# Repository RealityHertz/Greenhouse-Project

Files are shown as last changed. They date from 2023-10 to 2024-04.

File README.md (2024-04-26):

# Autonomous Greenhouse Project

## Executive Summary

With this project Team 2 proposes to create a greenhouse that can wirelessly and autonomously detect soil moisture, pH level, and nutrient level as well as carbon dioxide and nitrogen monoxide in the greenhouse's atmosphere along with the greenhouse's temperature and humidity. The greenhouse will also be able to autonomously detect the water level of an exterior water source and fill said reservoir when the level is too low as well as running a timed watering cycle for the plants. 

## Capabilities

This version of the project will be able to accurately measure the levels of nitrogen, phosphorus, and potassium in the greenhouse soil as well as the temperature, humidity, carbon dioxide, and nitrogen monoxide levels in the atmosphere. The project will also be able to detect the water level of an external reservoir that will alert when low and be able to refill when the alert is sent.

## Salient Outcomes

### 1. Soil Moisture, pH, and Nutrient Level Detection
- **Outcome:** Develop a system that provides real-time data on soil conditions, allowing for precise adjustments to watering schedules and nutrient applications. This could lead to optimized plant growth and reduced resource waste.

### 2. Atmospheric Monitoring (CO2 and NO2 Levels)
- **Outcome:** Implement sensors that continuously monitor and log the levels of CO2 and NO2. This data could be used to adjust ventilation, maintaining optimal air quality for plant health.

### 3. Temperature and Humidity Control
- **Outcome:** Create a responsive system that adjusts internal temperature and humidity based on preset thresholds. This could help in maintaining a stable environment that promotes plant health and productivity.

### 4. Water Level Monitoring and Reservoir Refilling
- **Outcome:** Design an automated system that detects low water levels in an external reservoir and alerts for manual intervention. This ensures a consistent water supply for the greenhouse, crucial for plant survival and growth.

### 5. Adjustable Lighting System
- **Outcome:** Implement a lighting system that can adjust the duration of grow light exposure based on Human-Machine Interface (HMI) inputs. This allows for flexible light management tailored to the growth stages and needs of different plant

### Documentation and Sign-offs
For detailed outcomes and progress on these subsystems, refer to the specific documentation and sign-offs provided in the project's [Documentation/Signoffs folder](https://github.com/RealityHertz/Greenhouse-Project/tree/main/Documentation/Signoffs). This folder contains detailed reports and approval documents that outline the performance and expectations for each subsystem.

## Project Demonstration & Images

[Demonstration Videos](https://github.com/RealityHertz/Greenhouse-Project/tree/main/Documentation/Images/Team2_Experimental_Videos)

### Lighting System Images

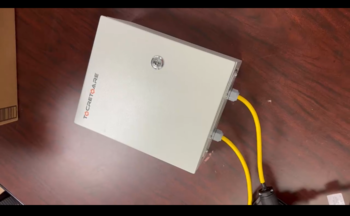
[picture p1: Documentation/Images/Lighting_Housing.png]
Lighting Housing


- The above image shows the housing for the lighting system as it is closed and being tested.

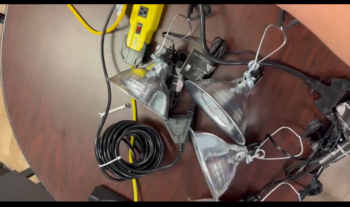
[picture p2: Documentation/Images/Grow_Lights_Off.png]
Grow Lights Off


- This image shows the lighting system's grow lights when they are powered off.

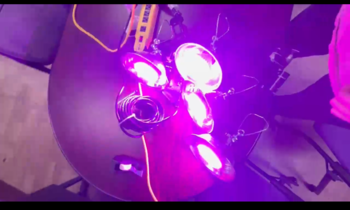
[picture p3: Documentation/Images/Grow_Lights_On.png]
Grow Lights On


- This shows the grow lights while powered on.

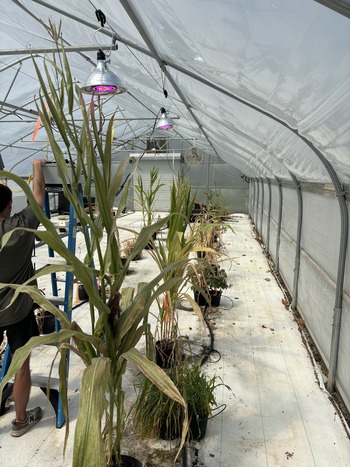
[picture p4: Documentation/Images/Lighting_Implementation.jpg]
Lighting Implementation


- This image shows the lighting system being implemented and tested within the greenhouse setting of the Hyder-Burks facility.

### PLC and HMI Images

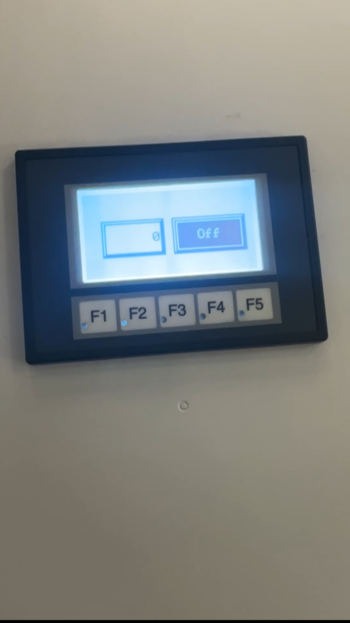
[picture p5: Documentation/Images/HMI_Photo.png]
HMI


- This shows the HMI as it rests within the PLC housing and is being tested.

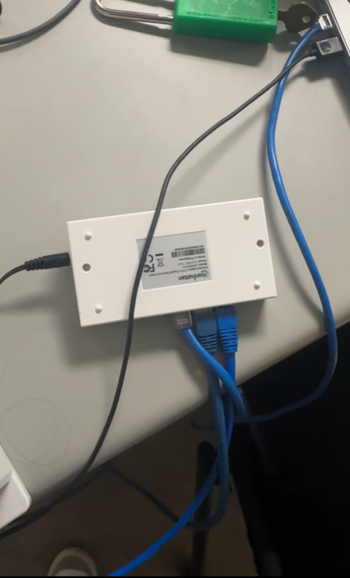
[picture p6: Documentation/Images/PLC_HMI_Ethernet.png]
PLC Ethernet Hub


- This image shows the ethernet hub that connects the PLC and HMI to an outside source for pushing of code and testing while powered on.

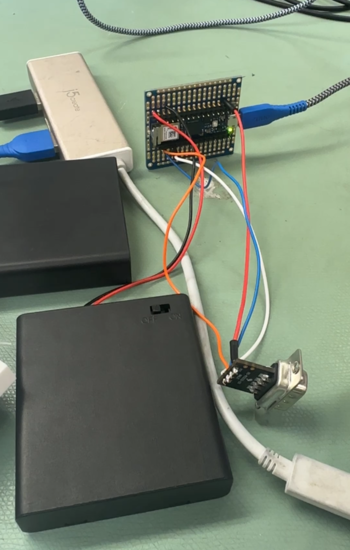
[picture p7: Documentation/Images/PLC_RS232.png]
PLC RS232 Translator
 

- The image above shows the RS232 to TTL translator module that allows the PLC to communicate with the Arduino pictured to allow for sending of commands and recieving of data.

### Water Level System Images

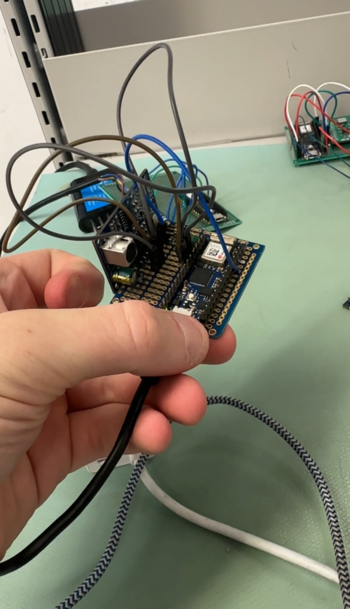
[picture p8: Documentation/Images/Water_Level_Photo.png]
Water Level Image


- Pictured above is the breadboard containing the water level sensor and the Arduino Nano 33 IoT for the water level system as it is being tested.

### CO2 and NO2 System Images

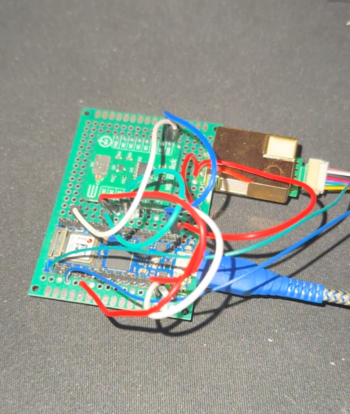
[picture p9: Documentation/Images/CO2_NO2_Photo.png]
CO2 and NO2 Image


- The above image shows the breadboard containing the carbon dioxide and nitrogen dioxide sensors for the CO2 and NO2 system as well as their connected Arduino. The nitrogen dioxide sensor is the green sensor pictured in the center of the image directly above the Arduino while the carbon dioxide sensor is the gold sensor located on the right hand side of the board.

### Temperature and Humidity System Images

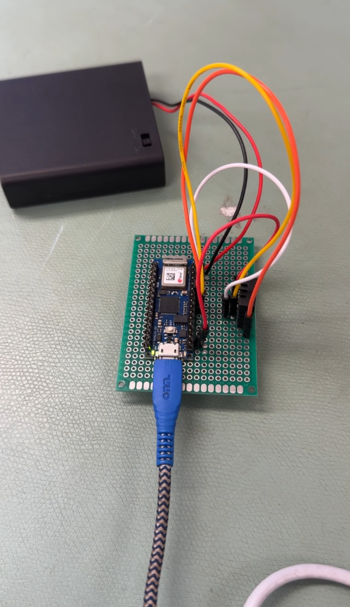
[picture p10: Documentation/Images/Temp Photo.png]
Temp and Humidity Image


- Pictured above is the temperature and humidity system with the transmitting Arduino pictured on the left of the board and the sensor itself pictured on the right as the small black box surrounded by wires.

### Nutrient System Images

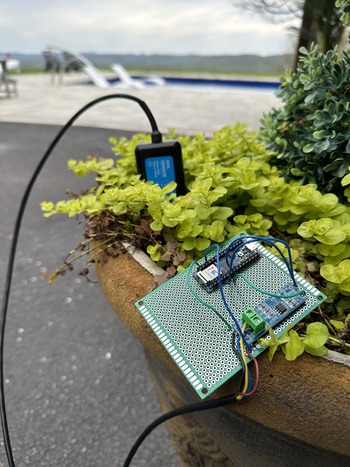
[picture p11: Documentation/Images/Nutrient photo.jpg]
Nutrient Image


- This image shows the nutrient monitoring system as it is being implemented in a pot of soil picturing the sensor placed in the soil, the Arduino for sending and recieving data and finally the MAX485 to TTL translator which is pictured on the far right of the board.

## About Us

### Team

Team 2 is a 5 member Capstone Design Project Team at Tennessee Technological University who began Version 1 of the Greenhouse Automation Project in the Fall semester of 2023. The group members are Robert Jones, Jared Hooker, Jaxson Billings, Bryan Rhoton, and Grant Hooper. All members contributed to the C02 and N02 Monitoring System.

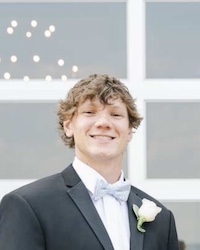
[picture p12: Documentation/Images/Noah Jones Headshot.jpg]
Noah Headshot

- **Robert Jones**
  - Electrical Engineering Major
  - Hardware
  - Controls
  - Lighting Control System
 
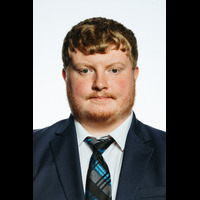
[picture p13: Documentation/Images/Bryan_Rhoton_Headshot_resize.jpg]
Bryan Headshot

- **Bryan Rhoton**
  - Computer Engineering Major
  - Soil Detection System

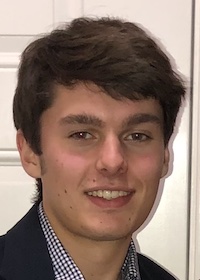
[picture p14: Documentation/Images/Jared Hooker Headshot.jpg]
Jared Headshot

- **Jared Hooker**
  - Electrical Engineering Major
  - Controls
  - Temperature & Humidity Monitoring System

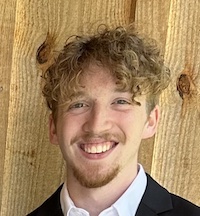
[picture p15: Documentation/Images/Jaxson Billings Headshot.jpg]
Jaxson Headshot

- **Jaxson Billings**
  - Computer Engineering Major
  - Programming
  - Communication and Display Subsystem

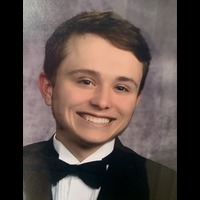
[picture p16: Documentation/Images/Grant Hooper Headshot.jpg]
Grant Headshot

- **Grant Hooper**
  - Electrical Engineer
  - Controls
  - Water Level Monitoring System

### Faculty Supervisor

The faculty advisor for the project is Jesse Roberts.

### Stakeholders

The customer for this project is the Agricultural Department at Tennessee Technological University. A scalable version of this design would be useful for agricultural researchers, farmers, and/or urban growers.

### Recognitions

Team 2 would like to recognize the sponsor for this project, EOSYS. They have worked closely with the group to help provide feedback, troubleshoot, and brainstorm ideas for the project. 

## Repo Organization

### [Reports](https://github.com/RealityHertz/Greenhouse-Project/tree/main/Reports)

Finalized reports can be found by going to the Reports folder or by clicking the link above.

### [Documentation](https://github.com/RealityHertz/Greenhouse-Project/tree/main/Documentation)

Group documentation can be found by going to the Documentation folder or by clicking the link above.

### [Software](https://github.com/RealityHertz/Greenhouse-Project/tree/main/Software)

Software can be found by going to the Software folder or by clicking the link above.

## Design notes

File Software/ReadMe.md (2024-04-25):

# Software Folder

This folder contains all of the software used in the Autonomous Greenhouse project. These files are required components representing background programming used in the subsystems within the greenhouse environment.

## Contents

- ArduinoIDE Folder
  -  Arduino_AHTXO
      -  File for DHT and AHT collection of data and BLE transmisson
  -  Arduino_CO2
      - File for MH-Z19B data collection and BLE transmisson
  -   Arduino_DHT
      - File for DHT20 data collection and BLE transmisson    
  -   Arduino_Lighting
      - Simple Digital Pin set high, delay, set low code to power the lighting   
  -   Arduino_NO2_w_ADC
      - File for MIKROE-3700 data collection and BLE transmisson   
  -   Arduino_NPK
      - File for NPK Sensor data collection and BLE transmisson
  -   Arduino_NPK_NoBLE
      - File for MH-Z19B data collection without BLE transmisson
  -   Arduino_NPK_NoBLE_From_Web
      - Test file for MH-Z19B data collection
  -   Arduino_RS232
      - File for transmisson through RS232 after data collection
  -   Arduino_Water_Level
      - File for distance sensor data collection and BLE transmisson and sends a true or false depending on how high or low the distance is
  -   Arduink_waterLevel
      - File for water level sensor data collection and BLE transmisson
  -   BLE_Scan_Test
      - File for the central Arduino that then sends the collected BLE data through RS232 to the PLC  
  -   NO2_SPI_Sensor
      -   File for MIKROE-3700 data collection and BLE transmisson through SPI.

## Usage

These software files represent the background programming that the subsystems need to function. This includes, but is not limited to, Arduino sleep pattern coding, sensor reading conversions, and sleep pattern timing. Refer to individual software directories for more information of each software's individual purpose and usage.

## File Formats

The software is provided in commonly used file formats compatible with the chosen arduino and sensors. Formats include `.c`, `.h`, and `.ino`.

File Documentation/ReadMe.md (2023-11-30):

# Documentation

The `Documentation` folder serves as a comprehensive repository of essential project documentation and artifacts for the Autonomous Greenhouse project. This README aims to provide guidance and an overview of the contents within this directory.

## Contents

### Signoffs

This directory contains markdown files for signoffs of subsystems. Each signoff document details the subsystem's purpose, constraints, buildable schematic, analysis, Bill of Materials (BOM), and more. Refer to the README in the "Signoffs" directory for detailed guidelines on creating and updating signoff files.

### Final Set of Prints (Final Design Artifacts)

All schematics and design artifacts, including 3D models, wiring schematics, PCB files, final BOM, datasheets, project poster, detailed project photos, and any additional relevant documents, are stored here.

#### 3D Models

Stored in `.stl` format, these models provide complete, buildable 3D representations of the various systems within the project.

#### Wiring Schematics

Electrical systems' wiring schematics, created using AutoCAD or AutoCAD Electrical, are stored here. Source files and PDF versions of the schematics must be included.

#### PCB Files

KiCad is used for all PCB design, with source files and complete gerber files included. PCB-related documents are housed within this section.

#### Final BOM

A PDF output of the Excel-based Bill of Materials (BOM) file along with the Excel file itself is included here.

#### Datasheet

This document contains vital information necessary for interfacing with the project, including power expectations, interfacing details, compliance information, experimental results, and their interpretations.

#### Project Poster

The project poster, visually representing key project details and components, is stored in this section.

#### Detailed Photos

A folder of detailed project photos provides visual documentation of the project's various aspects.

#### Additional Documents

Any other pertinent documents relevant to understanding, working on, or with the project are included in this section.

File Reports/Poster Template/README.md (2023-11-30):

# Autonomous Greenhouse Poster

## Contents

- Currently empty. Poster coming Spring 2024.

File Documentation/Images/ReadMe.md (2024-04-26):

# Images Folder

The `Images` folder contains visual assets utilized in the markdown files detailing subsystem designs and resources needed within the `Sign-offs` folder within the Autonomous Greenhouse project.

## Contents

The images are organized based on alphabetical order. They are used in various subsystem design markdown files. They aid in visually explaining and illustrating different components and concepts of the subsystems.

### Images

- **3D-artifact-CAPSTONE.png**
- **3D-artifact-sensor-CAPSTONE.png**
- **3D-artifact-topdown-CAPSTONE.png**
- **AA-100mA.png**
- **ArduinoNano33.png**
- **Breaker Datasheet.png**
- **CADHMISubsystemSchematic.jpg**
- **CADPLCSubsystemSchematic.jpg**
- **CADSchematicNitrogenSubsystem.jpg**
- **CADTemperature&HumidityDrawing.jpg**
- **CADUPDATED.png**
- **CO2graph.png**
- **Cad Final Update.png**
- **Final Drawing Line.png**
- **Final Relay Data.png**
- **Final Relay Pic.png**
- **HMI2DModel.PNG**
- **HMIMountingRearView.png**
- **HMIMountingSideView.png**
- **HMIScrewPlacement.png**
- **Jaxson Billings Headshot.jpg**
- **Lighitng Control Timing.png**
- **Mounting-Model.png**
- **NPK Sleep Mode.png**
- **NPK_Battery_Supply.png**
- **Noah Jones Headshot.jpg**
- **Nutrient_Off_Sim2.png**
- **Nutrient_On_Sim2.png**
- **Nutrient_Schematic_V7.png**
- **PLC 2D Model.png**
- **PLCPowerSupply2DCAD.PNG**
- **PPM.png**
- **PhopGraph.png**
- **PotaGraph.png**
- **Relay Datasheet.png**
- **RelayDiagram.png**
- **RelayPic.png**
- **SPIDataOutToINT.png**
- **Screenshot 2024-03-08 123324.jpg**
- **Tx to Int Code.png**
- **Updated paint.png**
- **VoltageGraph.png**
- **WaterLevelGraph.png**
- **Water_Level_Schematic.png**
- **pHGraph.png**
- **CO2_NO2_Photo.png**
- **Grow_Lights_Off.png**
- **Grow_Lights_On.png**
- **HMI_Photo.png**
- **Lighting_Housing.png**
- **Lighting_Implementation.jpg**
- **Nutrient Photo.jpg**
- **PLC_HMI_Ethernet.png**
- **PLC_RS232.png**
- **Temp Photo.png**
- **Water_Level_Photo.png**

## Usage

These images play a pivotal role in enhancing the understanding and visualization of the subsystem designs presented in the markdown files. Each subfolder corresponds to a specific subsystem and contains relevant images associated with that subsystem's design documentation.

## File Formats

The images are available in formats such as `.png`, `.jpg`, `.svg`, or other common image formats, ensuring compatibility across various markdown rendering platforms.

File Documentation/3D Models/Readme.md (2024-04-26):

# 3D Models Folder

This folder contains a collection of 3D models used in the Autonomous Greenhouse project. These models are integral components representing various elements used in subsystems within the greenhouse environment.

## Contents

- Mount for the water level monitoring system

## Usage

These 3D models serve specific purposes within the project, such as simulating greenhouse structures, equipment, or plant elements. Refer to the individual model directories for more detailed information on each model's application and usage.

## File Formats

The models are provided in commonly used file formats compatible with standard 3D modeling software. Format on all 3D models is `.stl`.

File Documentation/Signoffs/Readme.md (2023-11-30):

# Signoffs Folder

The `Signoffs` folder holds signoff markdown files for each subsystem within the Autonomous Greenhouse project. These files adhere to specific guidelines for submitting and updating signoffs as outlined below.

## Content

  - **CO2 & NO2 Monitoring Subsystem Signoff**
  - **Lighting Control Subsystem Signoff**
  - **Display Subsystem Signoff**
  - **Water Level Subsystem Signoff**
  - **PLC Subsystem Signoff**
  - **Nutrient Monitoring Subsystem Signoff**
  - **Temperature & Humidity Monitoring Subsystem Signoff**

## Sections in Signoff Markdown File

Each signoff markdown file must include the following sections:

### Function of the Subsystem

Explain the primary function and role of the subsystem. Clarify its atomic purpose as outlined in the conceptual design.

### Constraints

Detail the constraints for the subsystem, explaining the rationale behind each constraint. Constraints may arise from physics, other subsystem requirements, standards, ethics, or socioeconomic considerations.

### Buildable Schematic

Embed a clear and appropriately sized schematic directly into the markdown file as a JPEG image. Ensure the schematic contains all necessary details for someone unfamiliar with the design to build it. Upload the actual design artifacts (e.g., 3D models, CAD files, gerber files) to the documentation folder in the appropriate location.

### Analysis

Provide a comprehensive analysis of the design, demonstrating how it meets the constraints and functions as intended. Ensure the analysis is well-explained and convincing to the faculty supervisor.

### Bill of Materials (BOM)

Include a markdown table listing all components required for the design, along with the cost of each component and the total cost of the subsystem.

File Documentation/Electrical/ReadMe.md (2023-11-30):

# Electrical Folder

This folder contains electrical designs and schematics related to various subsystems within the Autonomous Greenhouse project.

## Subfolders

### Schematics

The `Schematics` subfolder houses detailed designs of individual electrical subsystems. Each subsystem's schematic is categorized and stored within its respective directory.

### Contents

- **Display Subsystem**
- **Nitrogen and Carbon Dioxide Monitoring Subsystem**
- **Lighting Control Subsystem**
- **Temperature and Humidity Monitoring Subsystem**

## Usage

These electrical schematics are crucial for understanding and implementing the respective subsystems within the autonomous greenhouse setup. Navigate into each subsystem directory for comprehensive information on the electrical designs.

## File Formats

The schematics are in file formats such as `.jpg`, `.png`, `.svg`, or other common formats, allowing easy viewing and reference.

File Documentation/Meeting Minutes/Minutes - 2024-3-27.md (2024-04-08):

 

# *Meeting Minutes – Greenhouse Project* 

**Location:**

Brown 320

**Date:**

Wednesday, April 3rd

**Time:**

2:30 PM

**Attendance:**

Noah Jones

Grant Hooper

Jaxson Billings

Jared Hooker

Bryan Rhoton

**Agenda Items**

1\. Update Jesse on Minimally Functioning Subsystems

**Action Items**

1\. Use Serial and Manual for PLC

2\. Communication for PLC

3\. How the PLC communicate from the bus to the Ladder Logic is completely dependent.

**Individual Items**

Brian Rhoton: Work on Functional Prototype Design.

Grant Hooper: Work on Functional Prototype Design. PLC Ladder Logic.

Noah Jones: Work on Functional Prototype Design.

Jared Hooker: Work on Functional Prototype Design.

Jaxson Billings: Work on Functional Prototype Design. Weekly Minutes.

Group: Meet with EOSYS

**Other Notes**

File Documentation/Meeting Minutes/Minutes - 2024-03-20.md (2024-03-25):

 

# *Meeting Minutes – Greenhouse Project* 

**Location:**

Brown 320

**Date:**

Friday, March 22th

**Time:**

2:30 PM

**Attendance:**

Noah Jones

Grant Hooper

Jaxson Billings

Jared Hooker

Bryan Rhoton

EOSYS

**Agenda Items**

1\. Functional Prototype Design Constraints

2\. Week 10 Minutes.

**Action Items**

1\. Make sure all subsystems are plugged up and commuicating in a non-trival manner. Box needs to be closed and lighting or everything turned off to open it.

2\. NO2 Sensor is Functional.

3\. Arduino's are communicating via BLE.

4\. CO2 Sensor is functional.

**Individual Items**

Brian Rhoton: Work on Functional Prototype Design.

Grant Hooper: Work on Functional Prototype Design. PLC Ladder Logic.

Noah Jones: Work on Functional Prototype Design.

Jared Hooker: Work on Functional Prototype Design.

Jaxson Billings: Work on Functional Prototype Design. Weekly Minutes.

Group: Meet with EOSYS

**Other Notes**

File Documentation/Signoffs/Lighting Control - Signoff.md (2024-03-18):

 

# *Detail Design: Lighting Control*
## **Team Members: Robert Jones**
## **Function of the Subsystem:**
The function of this subsystem is to have grow lights shine on the plants to help them in their growing process. The system will allow the full-spectrum light operating hours to be adjustable via the PLC and the programmable buttons on the HMI. The system will be controlled by an Arduino which is connected to the Programmable Logic Controller (PLC) subsystem to tell the lights when to turn on and off. 
## **Constraints:**
- **Lighting Timing**

	During a plant's photosynthesis process, they require between 12 and 16 hours a day of full spectrum light. On an average day, a plant inside of the greenhouse will only receive around 10 hours per day. [1] To combat this, the lights must be able to shine for a minimum of 2 hours per day.
- **Light Intensity**

	Most plants need between 200-400 µmol/m²/s of light intensity to help to achieve optimal plant growth. [2] To achieve this measure of success, the distance of the lights from the plants will have to be fully adjustable as the plants grow upward toward the lights.
- **Light Control**

	To make the lights controllable for the user, the HMI must give the user the ability to adjust how long the lights are on per day. This must be between 2 and 6 hours, based on the current weather conditions or any other factors that may reduce UV light on the plants.  

## **Buildable Schematic:**
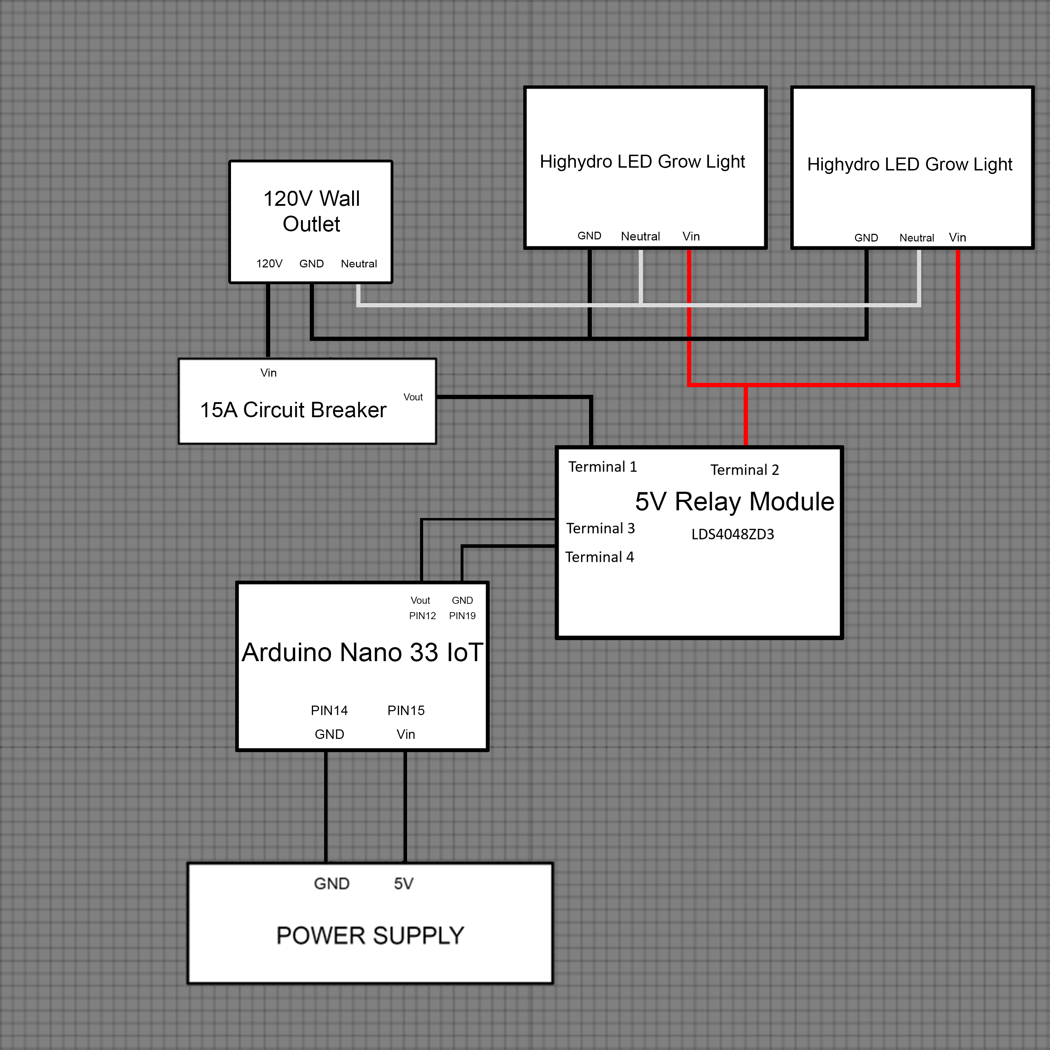
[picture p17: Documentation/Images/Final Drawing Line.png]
Lighting Control Schematic

*Figure 1. Buildable Schematic*

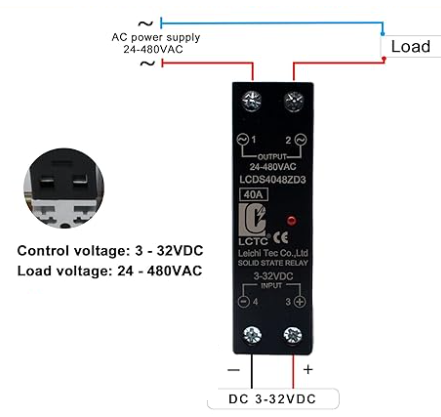
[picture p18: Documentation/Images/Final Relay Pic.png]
Relay Diagram


*Figure 2. Relay Diagram*

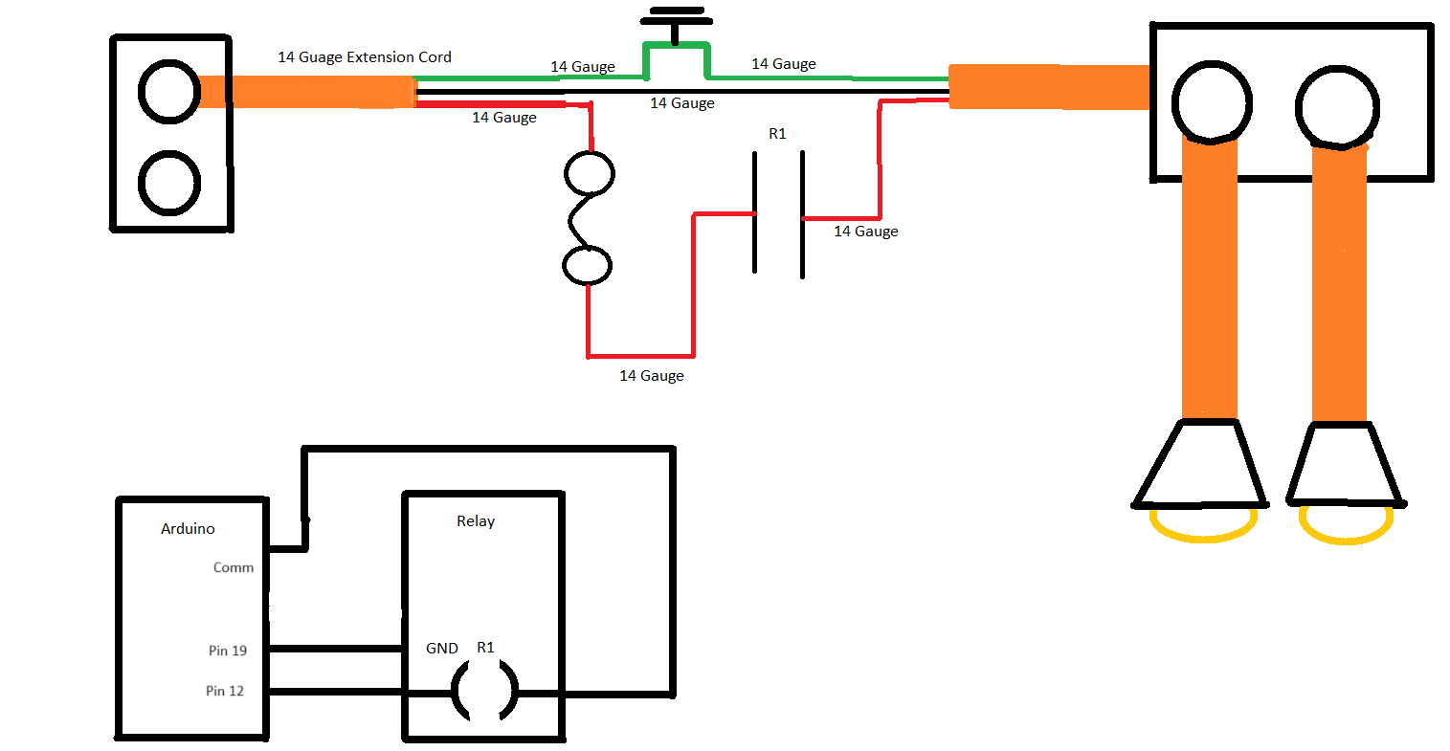
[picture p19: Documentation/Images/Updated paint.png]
Blueprint


*Figure 3. Connections*

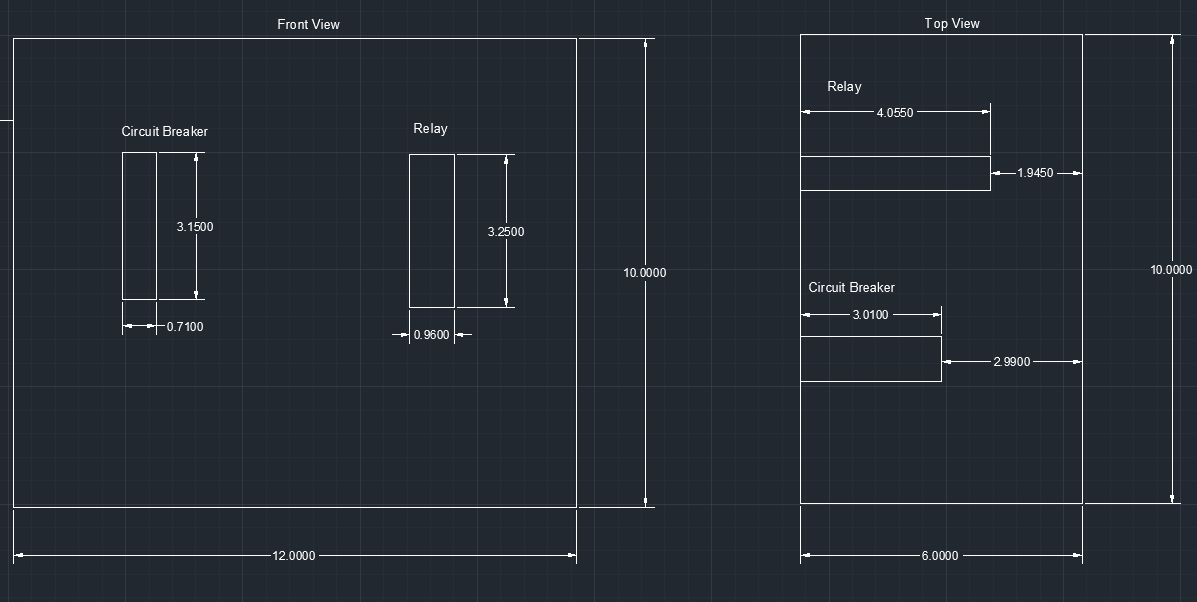
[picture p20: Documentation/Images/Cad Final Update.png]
NEMA 4X Enclosure Fit


*Figure 4. Enclosure Schematic. The figure on the right is the front view, with the left being the top view*
## **Analysis:**
- **Lighting Spectrum:**
1. The system uses four full-spectrum light bulbs which mimic UV rays from the sun. These lights will allow the plants to achieve optimal growth even when sunlight is not apparent.

- **Power Supply for Arduino Nano 33 IoT:**
 1. The power will be USB from a 120-volt wall outlet and will supply 5 volts to the Pin 15 on the Nano 33 IoT. The Pin 14 on the Nano 33 IoT will need to be connected to the ground from the USB ground wire.
 2. The USB cable and plug used have a max current of 1 amp and 2 amp respectively. This will allow for a safe current supply to the board.

- **Power Supply for Grow Bulbs:**
 1. The Arduino 33 Iot only has the ability to output 5V and a maximum current of 1 A, which will not satisfy the lights that need 100W.
 2.  A 15A breaker will be placed in the circuit to protect the wiring of the system. This breaker will meet the needs of the circuit based on: P=IV = 400W=I*120, therefore, the current is 3.33 amps which is below the rating of the 15A breaker.

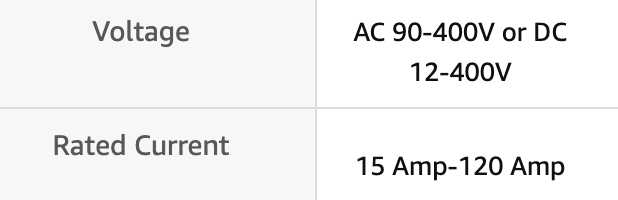
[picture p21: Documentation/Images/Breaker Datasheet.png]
Breaker Datasheet


*Figure 5. Breaker Datasheet*

 3. A relay will be placed in the circuit to control the main power while still allowing the Nano IoT to control the lights.[3]
 4. The relay has a maximum current rating of 40 A and a maximum voltage rating of 480 VAC. The system will be running on 120 VAC and 3.33A, therefore this relay meets the requirements.
 5. From the outlet, the power will be run through an extension cord to a NEMA 4x enclosure which will house the 15A circuit breaker and the relay.
 6. NEMA 4x was chosen due to its ability to keep out dust and direct sprays from water.
Here is an  excerpt from the Datasheet providing these requirements will be fulfilled:

Relay Data Sheet

*Figure 6. Relay Datasheet*

 7. Next, 14 gauge extension cords will be run from the relay to the lights. This will allow for safe power transfer due to the maximum amperage rating on the wire being 15 amps.[6]
 8. The positive wire of the extension cord, which is from the 120V wall outlet, will go into the breaker which will then come out of the other side of the breaker and into the common pin of the relay.
 9. The neutral wire will go straight to the extension cord which is connected to the lights, which allows for the unused power from the lights to return to the power supply.
 10. The ground wire will be grounded inside the box and also go to the lights, this is to ensure that the circuit will be shorted if there were to be a loose neutral or hot wire in the box.
 11. The bulbs will screw into an aluminum reflector lamp which will plug into the extension cord.

- **Enclosure Sizing and Mounting:**
1. The NEMA 4X enclosure is a 12x10x6 box which will house the circuit breaker and relay.
2. The circuit breaker is 0.71x3.15x2.95 and the relay is 0.96x3.25x3.01.
3. Therefore, these items will have a perfect fit inside of the enclosure and allow for plenty of space for the user to maneuver and to be able to run wires to each.
4. Each component inside of the enclosure will mount using DIN Mounting rails which are provided with the enclosure and both the relay and breaker can connect to.

- **Light Intensity:**
1. To give the plants the needed light intensity of 200-400 µmol/m²/s, the distance from the top of the plant to the light must be calculated.
2. Using the formula, Irradiance = Power/4π(r)^2, where P is equal to 100 watts for the bulb and r is equal to the distance of 5.5 feet from the top of the plant, the irradiance is equal to 318 µmol/m²/s, which is well within the range needed for cotton plants. [4]
3. Having the lights hung 5.5 feet above the plants will allow them to reach optimal growth, which is proven by the irradiance of the lights being 318 µmol/m²/s when 200-400 µmol/m²/s is needed. [2]
4. To achieve this constraint, the lights will be hung from a small chain and S-hook to be fully adjustable.

- **Control:**
1. To regulate the timing of light activation and deactivation, the HMI subsystem will feature four programmable buttons.
2. These buttons will enable users to adjust the duration for which the lights remain on and off, allowing for hour-by-hour increments in both directions.
3. For instance, if the preset timing is 2 hours for light activation and 8 hours for deactivation, the buttons will facilitate incremental adjustments, allowing users to increase or decrease each timing by one hour as needed.
4. To add further capabilities, a photocell will be added to the PLC to tell the system if it is day or night. This will in turn allow the PLC to know when the light should start the cycle that has been set by the user.

## **Bill of Materials:**
|Brand/Manufacturer|Part Name|Supplier|Part/Model Number|Quantity|Individual Price|Total|
|----|---|---|---|---|---|-----|
|LCLCTC|Relay Module|Amazon|B0BQ2RFW6G|1|$18.90|$18.90|
|Highydro|Full Spectrum Grow Light|Amazon|Grow Light|4|$21.99|$87.96|
|Arduino|Bluetooth Board|Amazon|Nano 33 IoT|1|$25.90|$25.90|
|VIVOSUN|4 Pack Lamp Aluminum Reflector E26|Amazon|B07H8G6PKX|1|$22.99|$22.99|
|DIHOOL|15 Amp Circuit Breaker|Amazon|B0BFF6CX2X|1|$13.99|$13.99|
|AIRIC|Cable Glands|Amazon|NPT 1/4" 20 Pieces|1|$11.99|$11.99|
|TOCRETOARE|NEMA 4x Enclosure|Amazon|12x10x6" Box|1|$49.99|$49.99|
|HONDERSON|10ft 14-3 Extension Cord|Amazon|3 Prong SJTW Heavy Duty Extension Cable|1|$12.99|$12.99|
|Maximm|30ft 14 Gauge Extension Cord with Multiple Outlets|Amazon|B0BT56KZCR|1|$32.99|$32.99|
|Leviton|Straight Blade Rubber Plug|Amazon|000-515PR-000|1|$7.25|$7.25|

## **References:**

[1]
Everbeam. “How Long to Leave UV Light on Plants: A Guide to Optimal Exposure Time.” Everbeam, shopeverbeam.com/blogs/news/how-long-to-leave-uv-light-on-plants-a-guide-to-optimal-exposure-time#:~:text=The%20distance%20between%20the%20plants%20and%20the%20grow. Accessed 13 Feb. 2024.

[2]
H. Chen et al., “Competition for Light Interception in Cotton Populations of Different Densities,” Agronomy, vol. 11, no. 1, p. 176, Jan. 2021, doi: 10.3390/agronomy11010176. [Online]. Available: http://dx.doi.org/10.3390/agronomy11010176
‌

[3]
Cruz, Terenz Jomar Dela. “How to Power Light Bulbs Using an Arduino with a Relay Module.” IoT Tech Trends, 19 Oct. 2022, www.iottechtrends.com/use-relay-module-with-arduino/.

[4]
How Close Should Grow Lights Be to Plants? 22 Apr. 2023, theindoornursery.com/blog/how-close-should-grow-lights-be-to-plants/#:~:text=In%20general%2C%20grow%20lights%20for%20mature%20plants%20should. Accessed 13 Feb. 2024.

[5]
Vanorio, Ame. “Growing Cotton: A Complete Guide on How to Plant, Grow, & Harvest Cotton.” MorningChores, 24 July 2019, morningchores.com/growing-cotton/.

[6]
National Electrical Code Basics: Sizing and protecting branch-circuit conductors - technical articles. EEPower. (n.d.). https://eepower.com/technical-articles/national-electrical-code-basics-sizing-and-protecting-branch-circuit-conductors

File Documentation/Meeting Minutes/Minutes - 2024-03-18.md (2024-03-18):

 

# *Meeting Minutes – Greenhouse Project* 

**Location:**

Brown 320

**Date:**

Monday, March 18th

**Time:**

2:30 PM

**Attendance:**

Noah Jones

Grant Hooper

Jaxson Billings

**Agenda Items**

1\. Sign-off/Revise Light Control Subsystem.

2\. Understand what is needed for Functional Prototype Design.

3\. Week 8 Minutes.

**Action Items**

1\. Lighting Subsystem Signed off.

2\. Make sure all subsystems are plugged up and commuicating in a non-trival manner. Box needs to be closed and lighting or everything turned off to open it.

**Individual Items**

Brian Rhoton: Work on Functional Prototype Design.

Grant Hooper: Work on Functional Prototype Design.

Noah Jones: Work on Functional Prototype Design. Blue LEDs are hard to get.

Jared Hooker: Help with other subsystems.

Jaxson Billings: Revise Sign-off Lighting Subsystem. Meeting minutes.

Group: Meet with EOSYS

**Other Notes**

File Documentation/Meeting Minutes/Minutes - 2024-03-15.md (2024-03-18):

 

# *Meeting Minutes – Greenhouse Project* 

**Location:**

Brown 320

**Date:**

Friday, March 6th

**Time:**

2:30 PM

**Attendance:**

Noah Jones

Jared Hooker

Grant Hooper

Bryan Rhoton

**Agenda Items**

1\. Sign-off/Revise Light Control Subsystem

2\. Sign-off/Revise Water Level Control Subsystem

3\. Week 8 Minutes.

**Action Items**

1\. HMI Subsystem Signed off.

2\. Nutirent Subsystem Signed off.

3\. Check in with EOSYS.

**Individual Items**

Brian: found a different sensor to measure at 5V and took away the regulator. Still communicates using RS485. Sensor will be running for 3 months according to the calculations. Jesse asked how long the batteries would actually last when considering battery decay.

 - “System is very vulnerable to the voltage dropping”. -Jesse

 - “Leaving tons and tons of charge in the batteries”

 - How can we boost the batteries to ensure that 5V is always attainable for an accepted amount of time? (3 months)

Grant: sensor communicates with PWM.

 - Find the pin on the Arduino that can be used for GPIO input PWM.

 - What is the frequency of the PWM?

 - Reverse engineer the code to understand how they got the frequency.

Noah: possibly draw the schematic on paper or in the Paint software

 - Break the ground to the box

 - Discussed the schematic with Jesse, he showed us an ideal way to make the schematic

Jared Hooker: Help with other subsystems.

Jaxson Billings: Revise Sign-off Lighting Subsystem. Meeting minutes.

Group: Meet with EOSYS

**Other Notes**

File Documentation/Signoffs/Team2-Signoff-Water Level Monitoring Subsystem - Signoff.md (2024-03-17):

# **Detail Design: Water Sensor**

## **Function of the Subsystem:**

The function of this subsystem is to relay the water levels to the Arduino via their respective sensors. The subsystem will use a sensor to determine whether the water reservoir is empty or not. If the reservoir is low on water, it will send data to the PLC for it to be refilled. The system is also able to be turned off for the user to manually water the plants.

## **Constraints:**

- **Arduino Nano 33 IoT**
  - The communication between the sensors and PLC system must be wireless. This will save time and money on wiring, while also allowing the system to be scalable.
  - The transfer of data between the sensors and the Arduino must be below 3 seconds for accurate and reliable monitoring of water level.
  - BLE (Bluetooth Low Energy) is lower in cost than the classic Bluetooth as BLE is currently rising in use and has market competition. BLE decreases the distance a signal can be transmitted, but the signals transmitted through the greenhouse will not be far. The use of BLE allows for a cost-efficient alternative compared to classic Bluetooth.

- **Water Level Sensor**
  - The transfer of data between the sensors and the Arduino must be below 3 seconds for accurate and reliable monitoring of water level.
  - Must be able to accurately sense when water level drops below 1/3 of the max to signal more water is needed to be added to the reservoir.
  - Must be durable enough to continue function while wet for an indefinite amount of time.
  - Must be cheap and easily replacable in the chance the user requires a new sensor.

## **Buildable Schematic:**

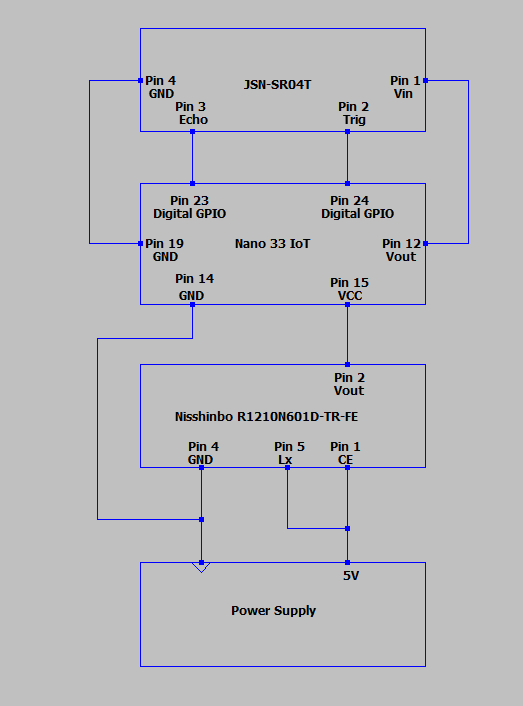
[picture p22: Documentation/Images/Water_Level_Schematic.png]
Buildable Schematic Water Level


_Figure 1. Wiring Schematic for Power to Sensor_ 
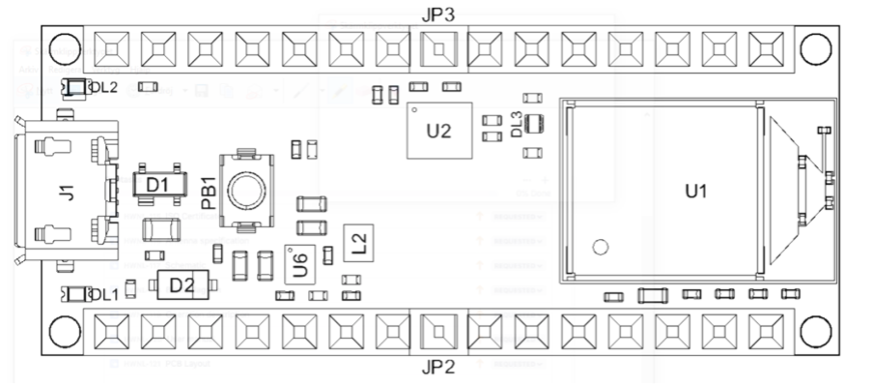
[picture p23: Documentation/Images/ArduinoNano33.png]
Arduino Nano 33


_Figure 2. Arduino Nano 33 IoT Board Topology_

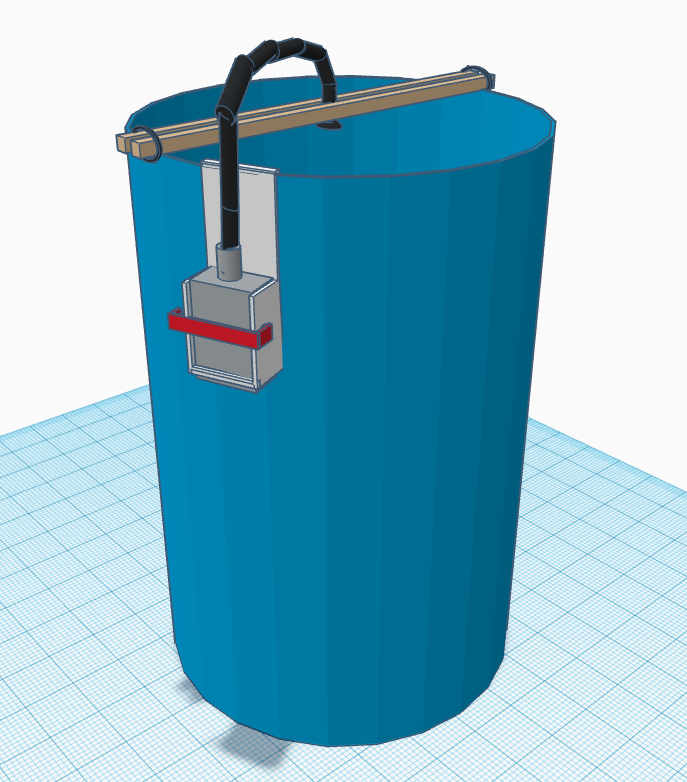
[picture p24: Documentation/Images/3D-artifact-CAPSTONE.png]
3D Artifact
.

_Figure 3. Set up for Subsystem_

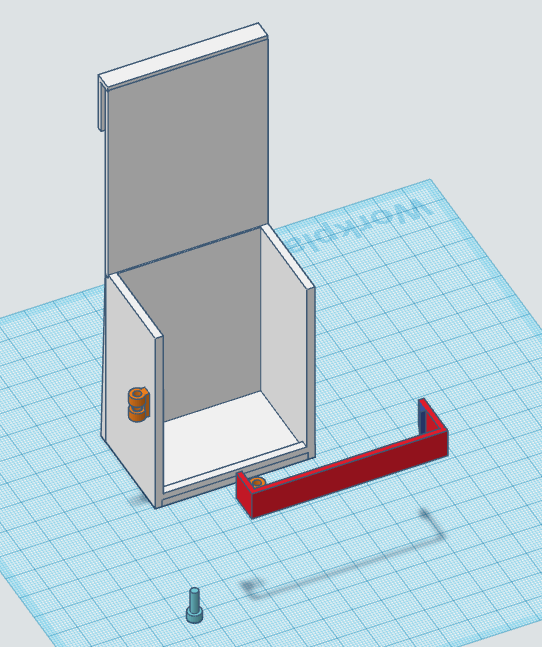
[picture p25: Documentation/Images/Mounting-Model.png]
Mounting Model


_Figure 4. 3D model  of desinged mount._

_For the model:  https://www.tinkercad.com/things/jwpPelM5zqh/edit?sharecode=Q2aPLBubOT7n5q68HoEgVgSHFNOAS2fjU0qmp6W8gsg_

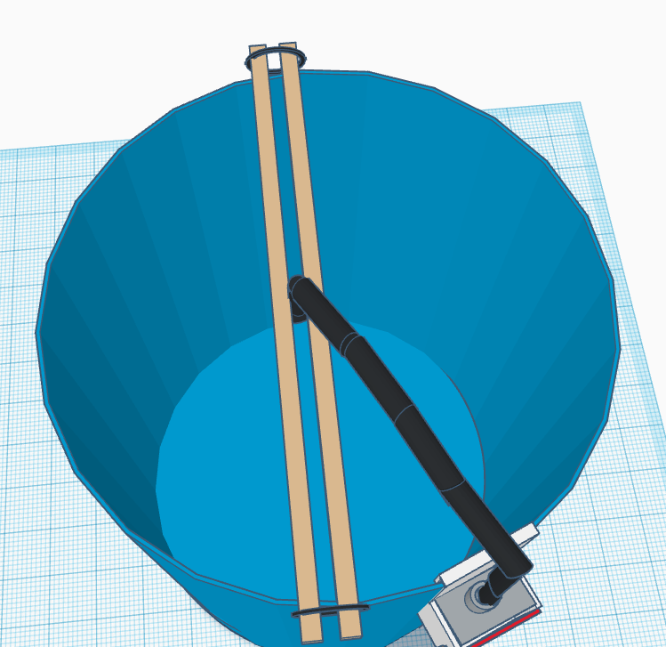
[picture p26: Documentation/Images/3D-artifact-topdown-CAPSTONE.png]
3D Artifact Top Down
.

_Figure 5. Top down view of subsystem set up_

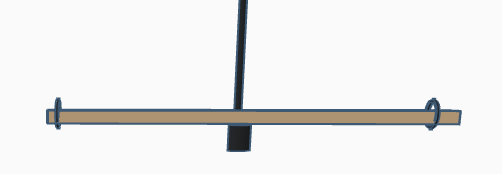
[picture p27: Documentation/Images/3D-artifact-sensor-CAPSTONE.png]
Holding Sensor
.

_Figure 6. Side view of the two dowels ziptied together holding up the sensor_

## **Analysis:**

- **Arduino Nano 33 IoT**
  1. The Arduino's BLE capabilities could be broadened by using an array of bluetooth extenders if required for larger projects.
  2. The Ardiuno will need to be cycled in and out of sleep mode to conserve battery life. This will be done by using the Arduino-Libraries Github and use the provided files and functions in the ArduinoLowPower folder. For example, we can use the function LowPower.sleep() and input the amount of time we want it to sleep in ms. Implementing this in a loop will then allow the microcontroller to continuously fall asleep and wake up for the desired time. We have decided to do a system where the Ardiuno runs for 10 seconds for every 5 minutes. [1] [2]
  3. BLE (Bluetooth Low Energy) is lower in cost than the classic Bluetooth as BLE is currently rising in use and has market competition. BLE decreases the distance a signal can be transmitted, but the signals transmitted through the greenhouse will not be far apart. The use of BLE allows for a cost-eﬃcient alternative compared to standard Bluetooth.

  - **Power Supply for Arduino Nano 33 IoT**
    - The power used will need to supply 5 volts to the Pin 15 on the Nano 33 IoT.
    - The Pin 14 on the Nano 33 IoT will need to be connected to the ground from the power supply.
    - The Arduino uses 28mA in on mode and 6mA in sleep mode.
    - The JSN-SR04T draws 30mA at 5V while on and 5 mA in a dormancy state.
    - The converter has a current draw of 0.09mA.
    - The batteries would have a realistic voltage drop off point of 2200mAh according to the graph below.
    - The system is on for 10 seconds every 5 minutes leading to a duty cycle of (10s / (5min * 60s)) = 0.0333
    - In "on" mode the system uses a total of 28mA + 30mA + 0.09mA = 58.09mA when the duty cycle is applied this leads to an average current draw of 58.09mA * 0.0333 = 1.936mA.
    - In "sleep" mode the system uses a total of 6mA + 5mA + 0.09mA = 11.09mA when the duty cycle is applied this leads to an average current draw of 11.09 * 0.9667 = 10.72mA.
    - There would be a total average current draw of 10.72mA + 1.936mA = 12.657mA leading to a battery life of 2200mAh / 12.657mA = 173.821 hours.
    - Since we have an expected battery usage of 86.7% we will realistically see a battery life of (173.821 * 0.867) = 150.65 hours or 6.28 days.
   
- **DC to DC Converter - Nisshinbo R1210N601D-TR-FE**
  
   1. The converter takes an input voltage range of 0.8-8V and produces a constant output of 6V ±0.15V.
   2. This is within the range of input voltage for the Arduino Nano 33 IoT and reduces the risk of having too little voltage for the Arduino as the battery charges dissipate.
   3. Since the minimum input voltage of the converter is 0.8V this means that the system will be able to operate until the power supply voltage drops below 0.2V per battery which means that roughly ((1.5V-0.2V)/1.5V) = 0.867 or 86.7% of the individual battery's supply is used before needing to be replaced.

- **JSN-SR04T**
  1. In order for the sensor to work, the JSN-SR04T must be on for at least 10 ms, which is 1/100 of the time its planned to be briefly turn on.
  2. The sensor has a range of 25cm - 4m.
  3. The sensor will use a 40kHz ultra sonic waves to determine height from the top of the resevoir by reading how long it takes for an ultra sonic wave to return. (The height of the reservoir) - (measured distance) = water level.
    - When the wave is returned, a pulse will be sent to the arduino whos length is proportional to the distance. The pulseIn() function from the Ardunio library will read this pulse and do the distance calculations.
        - The pulseIn() function looks like so: pulseIn(X, Y) where X is the observed variable and Y is either HIGH or LOW. When the function is called it looks at variable X and waits for it to toggle to Y (in this case, we will use HIGH so it will look for a toggle from LOW to HIGH). When this happens, a timer is started in milliseconds. The timer stops when the variable is toggled again. The function then outputs the time in milliseconds the variable was toggled for. 
    - Distance = (high level time) x (speed of sound in medium) x 0.5.
        - The speed of sound 340 m/s.
        - Therefore, the distance calculated by code will end up being (the high level time) * 170 m/s, giving the result in meters.
        - The pulseIn function used to read the duration of the sound wave requires the pulse to be 10 microseconds - 3 minutes. It takes sound well over 10 microseconds to travel 25 cm and its fast enough to travel and return 4 m in under 3 minutes.
        - This being said, the data will be read in under the 3 second prerequisite, due to the speed at which the echo will be received.
        - The units of measurement may also be changed between centimeters and inches in order for an easy to read result. It will be changed in code, given the unit for speed of sound in the medium is converted.
  4. The sensor is only $12.99 and waterproof making it a good fit for a durable and cheap option in the case of wear, tear, or mishaps.
 
  - **Power Supply for JSN-SR04T**
    - The JSN-SR04T will connect to the Nano 33 IoT's Pin 12 supplying 5 volts to the sensor, the Nano 33 IoT's pin 19 for ground, and the Nano 33 IoT's pins 23 and 24 for sending data.
    - The working voltage will be 5V
- **Water Levels**
  - The sensor will float on the water and send a signal to the Arduino 33 IoT saying whether the water level is below 1/3 of the max or not.
  - When the JSN-SR04T reads a distance that is equal to or less than the target height of 1/3 max, this will flag the PLC system.

- **Placement and Enclosure**
  - The enclosure will be set up using a desgined mount on the side of the resevoir using a cable gland to transport the wire out. Inside the enclosure will be the battery pack and the breadbaord. The wire for the sensor will then run out and over the reservoir. Two wooden dowels will be ziptied toegther with the sensor in between to hold the sensor over the center of the reservoir. 

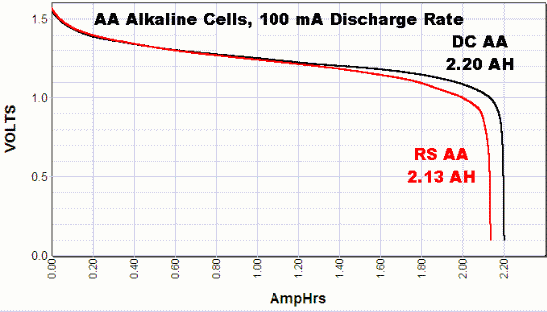
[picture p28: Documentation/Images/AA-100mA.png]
Battery Dropoff


_Figure 7. Duracell(DC) vs. Radio Shack(RS) AA battery voltage dropoff at 100mA current draw_
_Source: Adapted from [3]_

## **Bill of Materials:**

|Brand/Manufacturer|Part Name|Supplier|Part/Model Number|Quantity|Individual Price|Total|
|----|---|---|---|---|---|-----|
|Arduino|Bluetooth Board|Arduino|Nano 33 IoT|1|$25.50|$25.50|
|LAMPVPATH|4 AA Battery Holder|Amazon|B07L9M6VZK|1|$7.49|$7.49|
|Duracell|AA Batteries|Amazon|DURMN1500B10Z|1|$8.79|$8.79|
|DIYmore|Water Level Sensor|DIYmore|JSN-SR04T|1|$12.99|$12.99|
|Polycase|Enclosure|Polycase|SK-18 Enclosure with Knockouts 5.12 x 3.70 x 2.24 in|1|$20.92|$20.92|
|Polycase|Cable Gland|Ploycase|CG3 Gray Cable Glands 1.53 x 1.19 x 1.19in|1|$2.86|$2.86|
|Qunqi|Breadboard|Amazon|Qunqi 400 tie Point Experiment Mini Breadboard 5.5×8.2×0.85cm|1|$5.99|$5.99|
|Madison Mill|Dowel|Lowes|Madison Mill 0.75-in dia x 36-in L Square Poplar Dowel|2|$3.98|$7.96|
|Tin-N-Lock|Ziptiews|Amazon|Tie-N-Lock 8" Heavy Duty Nylon Cable Ties, 50 lb Test, 100 PC, Black|1|$1.21|$1.21|
| Nisshinbo | 6V dc to dc converter | Arrow.com | R1210N601D-TR-FE | 5 | $0.48 | $2.39 |

**References**

[1] “Arduino Low Power - Arduino Reference,” www.arduino.cc, Nov. 08, 2023).
‌<https://www.arduino.cc/reference/en/libraries/arduino-low-power/>

[2] O. Staquet, "Arduino-Nano-33-IoT-Ultimate-Guide," github.com [Online]. Available: https://github.com/ostaquet/Arduino-Nano-33-IoT-Ultimate-Guide/blob/master/SavePowerSleeping.md. [Accessed Feb. 14, 2024].

[3] PowerStream. "Discharge tests of AA Batteries, Alkaline and NiMH". (Feb. 7, 2023). Accessed: Mar. 7, 2024. [online]. Available: https://www.powerstream.com/AA-tests.htm

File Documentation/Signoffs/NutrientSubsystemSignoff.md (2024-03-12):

# *Detail Design: Nutrient Controller*
## **Function of the Subsystem:**
The function of this subsystem is to monitor the concentration of nutrients in the soil,
the pH balance of the soil, and the hydration level of the soil. This 
subsystem will use a sensor to detect hydration, pH balance, and nutrient concentration of the soil and relay that information to the 
PLC's Nano 33 IoT via BLE connection and then to the PLC itself via an ethernet cable from the connected Nano 33 IoT.
## **Constraints:**
- **Arduino Nano 33 IoT**

  1. The communication between the sensors and PLC must be wireless. This will save time and money on wiring, while also allowing the system to be scalable, meaning if the greenhouse was to be expanded then this subsystem would be easily expanded to account for more plants.
  2. The transfer of data between the sensors and the Arduino must be below 3 seconds for accurate and reliable monitoring of the different nutrient levels in the soil as well as the soil hydration and pH balance, and to allow plenty of time for communication with the PLC while looping in and out of sleep mode.
  3. 	The system needs to be capable of wirelessly communicating the collected data back to the PLC in an inexpensive, yet reliable way.
  4. 	The Arduino must support serial communication between itself and the rs485 translator.

- **Soil NPK and Moisture Sensor - CWT-SOIL-NPKPHCTH-S**

  1. The CWT-SOIL-NPKPHCTH-S needs between 4.5-30V to operate effectively.
  2. The sensor must turn on every 5 minutes in order to measure NPK levels, soil moisture, and pH balance.
  3. Must accurately measure soil moisture in a range of 0-100% to allow for optimum plant growth with ±3% to ±5% accuracy.
  4. Must accurately measure nitrogen levels in the soil within a range of 50-300mg/kg to allow for optimum plant growth with no more than ±10% accuracy. [1]
  5. Must accurately measure phosphorous levels in the soil within a range of 5-90mg/kg with no more than ±10% accuracy. [1]
  6. Must accurately measure potassium levels in the soil within a range of 50-240mg/kg with no more than ±10% accuracy. [1]
  7. Must accurately measure soil pH levels within a range of 5-8.5pH with an accuracy of ±0.01 pH to ±0.5 pH. [1]

## **Buildable Schematic:**
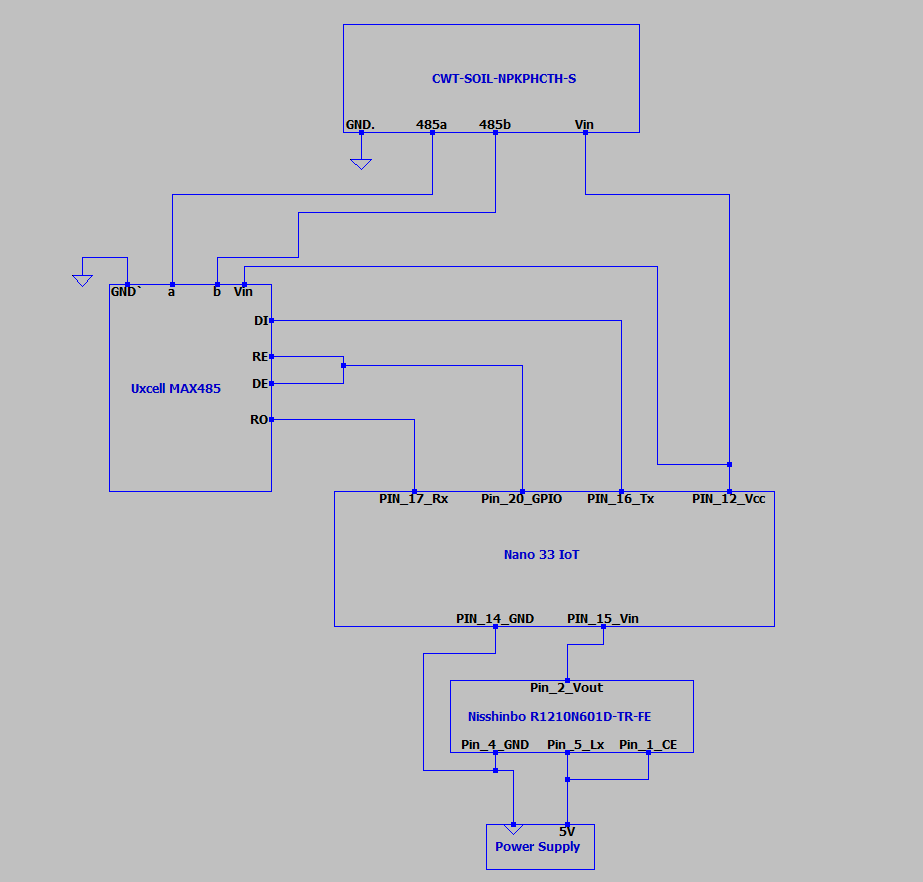
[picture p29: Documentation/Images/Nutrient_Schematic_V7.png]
Nutrient Schematic


*Figure 1. Buildable Schematic for Powering Arduino and Sensors*

## **Analysis:**
- **Arduino Nano 33 IoT**
  
   1. The Arduino will communicate with the sensors via a serial connection through the UXCELL Max485 translator and then to the plc via a seperate connected Nano 33 IoT which will be communicated with through BLE.
   2. The Ardiuno will need to be cycled in and out of sleep mode to conserve battery life. This will be done by using the Arduino-Libraries Github and use the provided files and functions in the ArduinoLowPower folder. For example, we can use the function LowPower.sleep() and input the amount of time we want it to sleep in ms. Implementing this in a loop will then allow the microcontroller to continuously fall asleep and wake up for the desired time. We have decided to do a system where the Ardiuno runs for 10 seconds for every 5 minutes. [2]
   3. Using Bluetooth Low Energy (BLE) allows for a cost efficient manner to transmit data throughout the greenhouse. A disadvantage of BLE is the decreased distance that information can be transmitted. Most BLE devices can trasmit/recieve data at a max rate of 50 meters [3]. However, the distance between the Arduino and the PLC will only be 15 feet, or 4.57 meters.
   4. The Arduino Nano 33 IoT contains both USART Rx and Tx pins, connected as shown in the figure above, to support the serial connection to the rs485 translator.
 
- **Soil NPK and Moisture Sensor - CWT-SOIL-NPKPHCTH-S**
   1. The sensor will be supplied 5V from the Arduino pin 12, which provides a 5V output, this will allow the sensor to be enabled and disabled as the Arduino cycles through sleep cycles.
   2. The sensor has a response time of less than 1 second and it will be enabled for 10 seconds every 5 minutes to allow the system time to commumicate with the PLC.
   4. The sensor measures soil moisture with a range of 0-100% with an accuracy of ±2% within the 0-50% moisture range and ±3% within the 50-100% range and a resolution of 0.10%.
   5. The sensor measures nitrogen levels within a range of 1-1999mg/kg with an accuracy of ±2% full scale and a resolution of 1mg/kg.
   6. The sensor measures phosphorus levels within a range of 1-1999mg/kg with an accuracy of ±2% full scale and a resolution of 1mg/kg.
   7. The sensor measures potassium levels within a range of 1-1999mg/kg with an accuracy of ±2% full scale and a resolution of 1mg/kg.
   8. The sensor measures pH within a range of 3-9pH with an accuracy of ±0.3pH and a resolution of 0.01pH.

- **DC to DC Converter - Nisshinbo R1210N601D-TR-FE**
  
   1. The converter takes an input voltage range of 0.8-8V and produces a constant output of 6V ±0.15V.
   2. This is within the range of input voltage for the Arduino Nano 33 IoT and reduces the risk of having too little voltage for the Arduino as the battery charges dissipate.
   3. Since the minimum input voltage of the converter is 0.8V this means that the system will be able to operate until the power supply voltage drops below 0.2V per battery which means that roughly ((1.5V-0.2V)/1.5V) = 0.867 or 86.7% of the individual battery's supply is used before needing to be replaced.
 
- **Power Analysis**
  
    1. The power is routed through the Arduino so that the sensor may be cycled on and off as the Nano 33 IOT enters and exits sleep mode, while the Arduino is in sleep mode it does not produce a high enough voltage for any of the systems components to function so they are all essentially powered off.[4]
    2. The Arduino will be cycled out of sleep mode for 10 seconds every 5 minutes leading to the sensors using (10s/3600s) for the milliwatt hour calculations, or 10 seconds per hour, and (5min/60min) for the average power consumption calculations from the 5 minute cycle.
    3. The system is powered by 4 AA batteries each supplying 3500mAh and 1.5V.
    4. The uxcell MAX485 has a current draw of <5ma in on mode and 0.3mA in sleep mode.
    5. The CWT-SOIL-NPKPHCTH-S has a max power usage of 500mW at 24V giving us (500mw/24V) = 20.83mA current draw and has a current draw of 4mA in sleep mode [5].
    6. The Nisshinbo R1210N601D-TR-FE uses 0.09mA at 6V.
    7. In the simulations below the battery and converter are shown as sinusoidal voltage sources to simulate the decay of the battery and the effeciency of the converter respectively.
    8. The Arduino is modeled as a 5V voltage source to simulate the Arduino's 5V output pin.
    9. The duty cycle of the components would be (10s / (5min * 60s)) = 0.0333 because the system is only turned on for 10 seconds every 5 minutes.
    10. Therefore the Ardunio has an current draw of 28mA in on mode and 6mA in sleep mode.
    12. According to the simulations below the system has a current draw of 25.83mA in on mode with additional loads from the Arduino and the converter giving a total current draw of 25.83mA + 28mA + 0.09mA = 53.92mA in on mode.
    13. According to the simulations below the system has a current draw of 25.83mA in on mode with additional loads from the Arduino and the converter giving a total current draw of 4.3mA + 6mA + 0.09mA = 10.39mA in off mode.
    14. When applying the duty cycle this gives us an average current consumption of (53.92mA * 0.0333) + (10.39mA * 0.9666) = 11.841mA.
    15. This means that the batteries would last for 2200mAh / 11.841mA = 185.795 hours and with an expected battery usage of 86.7% we will realistically see a battery life of (185.765 * 0.867) = 161.08 hours or 6.71 days.

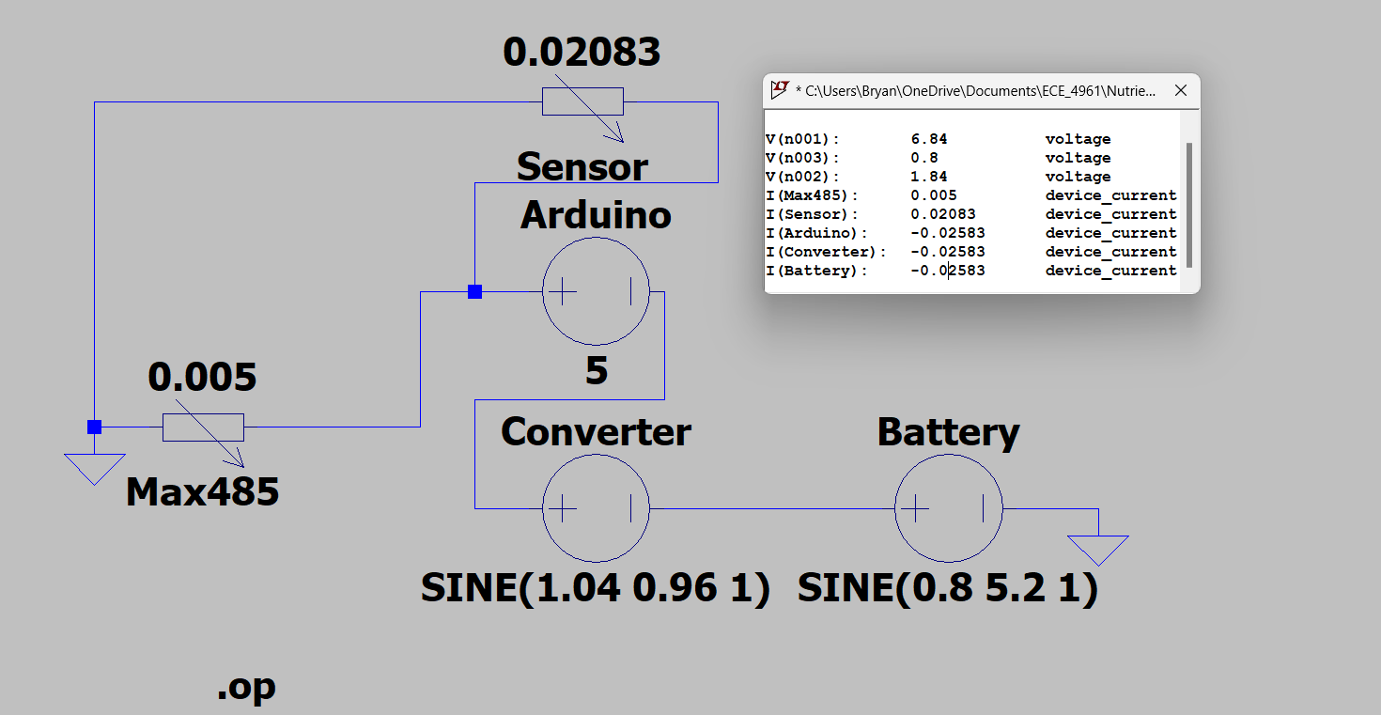
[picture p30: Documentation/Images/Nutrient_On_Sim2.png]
Nutrient On Sim
  

  *Figure 2. LTSpice Simulation for nutrient system in on mode using current load components (all current measurements in amperes)*

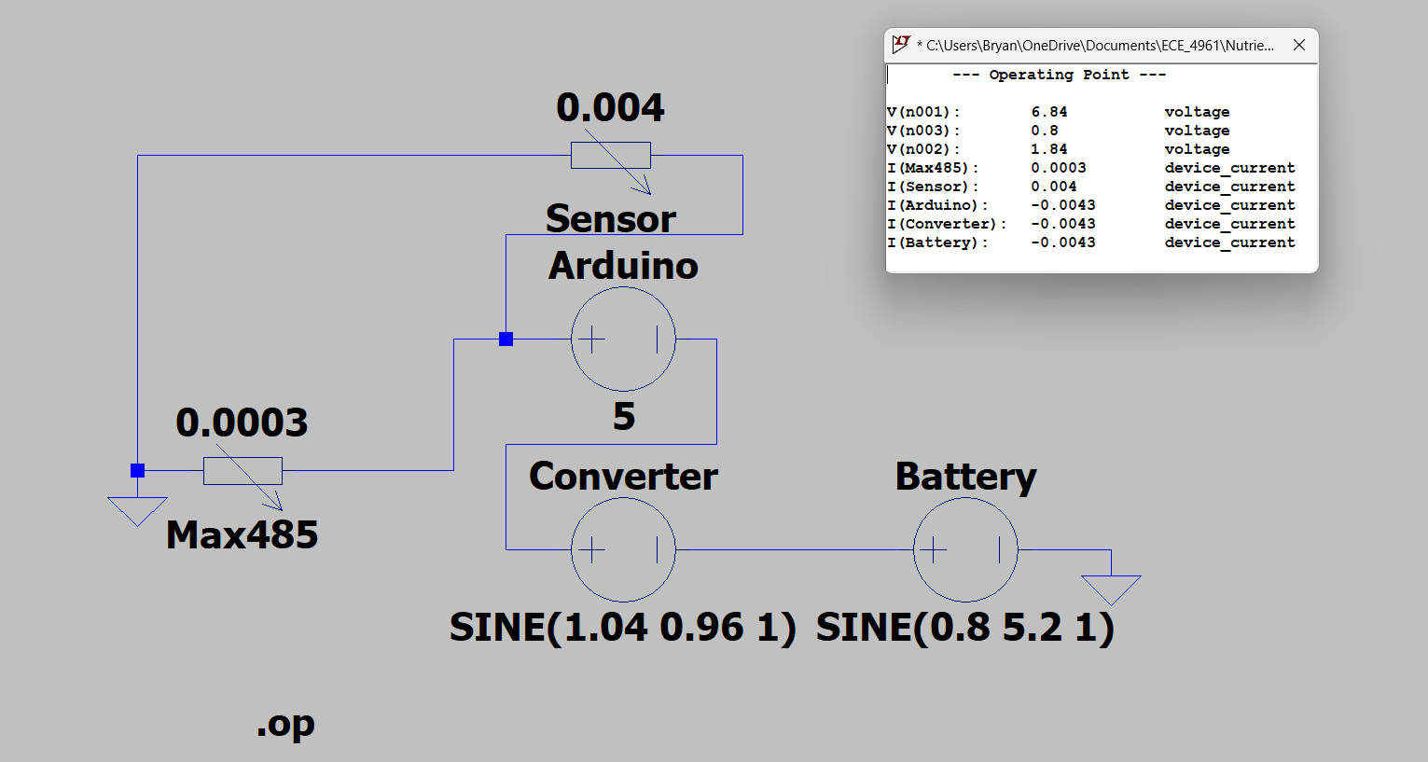
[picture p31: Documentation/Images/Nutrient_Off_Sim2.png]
Nutrient Off Sim
  

  *Figure 3. LTSpice Simulation for nutrient system in sleep mode using current load components (all current measurements in amperes)*
  
  Battery Dropoff

  *Figure 4. Duracell(DC) vs. Radio Shack(RS) AA battery voltage dropoff at 100mA current draw*

  *Source: Adapted from [6]*
 
## **Bill of Materials:**
| Brand/Manufacturer | Part Name | Supplier | Part/Model Number | Quantity | Units | Unit Cost | Cost |
| :--- | :--- | :--- | :--- | :--- | :--- | :--- | :--- |
| Arduino | Blue-tooth board | Arduino | Nano 33 IoT | 1 | 1 | $25.50 | $25.50 |
| ComWinTop | 7 in 1 Soil Probe | ComWinTop | CWT-SOIL-NPKPHCTH-S | 1 | 1 | $81.39 | $81.39 |
| Uxcell | RS485 Instrument Interface Module | Amazon | MAX485 TTL | 1 | 1 | $6.99 | $6.99 |
| LAMPVPATH | 4 AA Battery Holder | Amazon | B07L9M6VZK | 1 | 2 | $7.49 | $7.49 |
| Duracell | AA Batteries | Amazon | DURMN1500B10Z | 1 | 10 | $8.79 | $8.79 |
| Nisshinbo | 6V dc to dc converter | Arrow.com | R1210N601D-TR-FE | 5 | 5 | $0.48 | $2.39 |

## **References:**

[1] L.-Z. Liang et al., ‘Excessive application of nitrogen and phosphorus fertilizers induces soil acidification and phosphorus enrichment during vegetable production in Yangtze River Delta, China’, Soil Use and Management, vol. 29, 06 2013.

[2] “Arduino Low Power - Arduino Reference,” www.arduino.cc, Nov. 08, 2023).
‌<https://www.arduino.cc/reference/en/libraries/arduino-low-power/>

[3] “Advantages of BLE (Bluetooth Low Energy) | disadvantages of BLE (Bluetooth Low Energy),” www.rfwireless-world.com. https://www.rfwireless-world.com/Terminology/Advantages-and-Disadvantages-of-BLE-Bluetooth-Low-Energy.html

[4] O. Staquet, "Arduino-Nano-33-IoT-Ultimate-Guide," github.com [Online]. Available: https://github.com/ostaquet/Arduino-Nano-33-IoT-Ultimate-Guide/blob/master/SavePowerSleeping.md. [Accessed Feb. 14, 2024].

[5] ComWinTop, "RS485 4-20mA Soil Temperature Humidity Moisture Conductivity EC PH Sensor", ComWinTop, https://store.comwintop.com/products/rs485-4-20ma-soil-temperature-humidity-moisture-conductivity-ec-ph-sensor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

[6] PowerStream. "Discharge tests of AA Batteries, Alkaline and NiMH". (Feb. 7, 2023). Accessed: Mar. 7, 2024. [online]. Available: https://www.powerstream.com/AA-tests.htm

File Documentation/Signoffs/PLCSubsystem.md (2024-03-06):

# *Detail Design: PLC Subsystem*

## **Function of the Subsystem:**
The function of this subsystem is to receive data from the various sensors and relay that information to the HMI display. This system will also send commands to the various subsystems to change behaviors according to the PLC code.

## **Constraints:**

|Segment|Number|Constraint Description|
|---|-|---|
|PLC|1|The PLC scan time shall be able to scan fast enough to accommodate the desired sampling rate for all subsystem sensors. These sensors will be sending data every 5 minutes|
|PLC|2|The PLC shall have a compatible communication ports to allow for avaliable programming|
|PLC|3|The PLC shall be able to operate in 30% to 95% relative non–condensing humidity to ensure its suitability for deployment in greenhouse environmental conditions without risking damage due to moisture [2]|
|PLC|4|The PLC shall be able to input data from at least 3 Arduino Nano 33 IoT|
|PLC|5|The PLC shall be able to log data every hour for at least 1 month|
|Power Supply|6|The power supply  shall incorporate overcurrent protection and overvoltage protection to provide protection mechanisms for safeguarding connected equipment and ensuring the reliability of the power distribution system|

## **Buildable Schematic:**

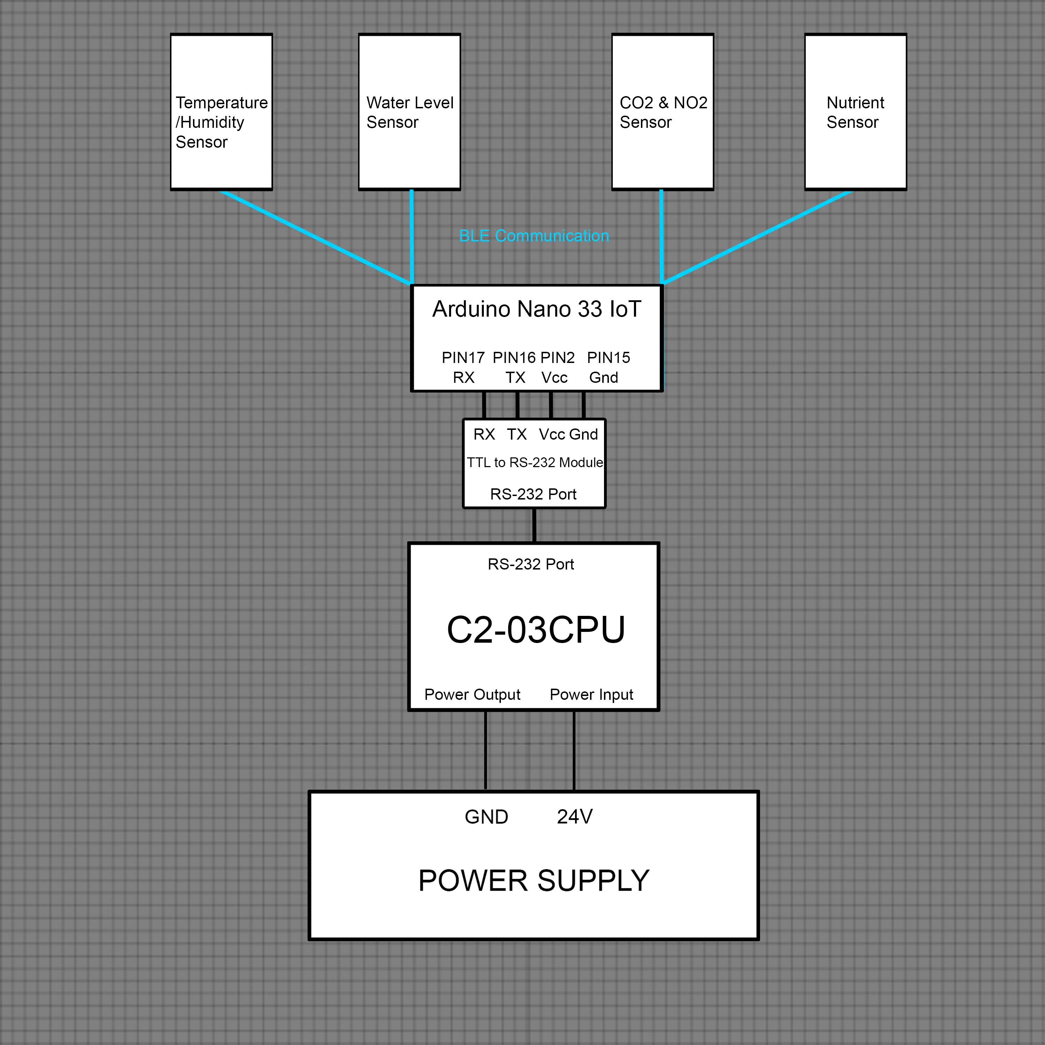
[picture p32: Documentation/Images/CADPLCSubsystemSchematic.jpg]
PLC Design


*Figure 1. PLC Subsystem Design*

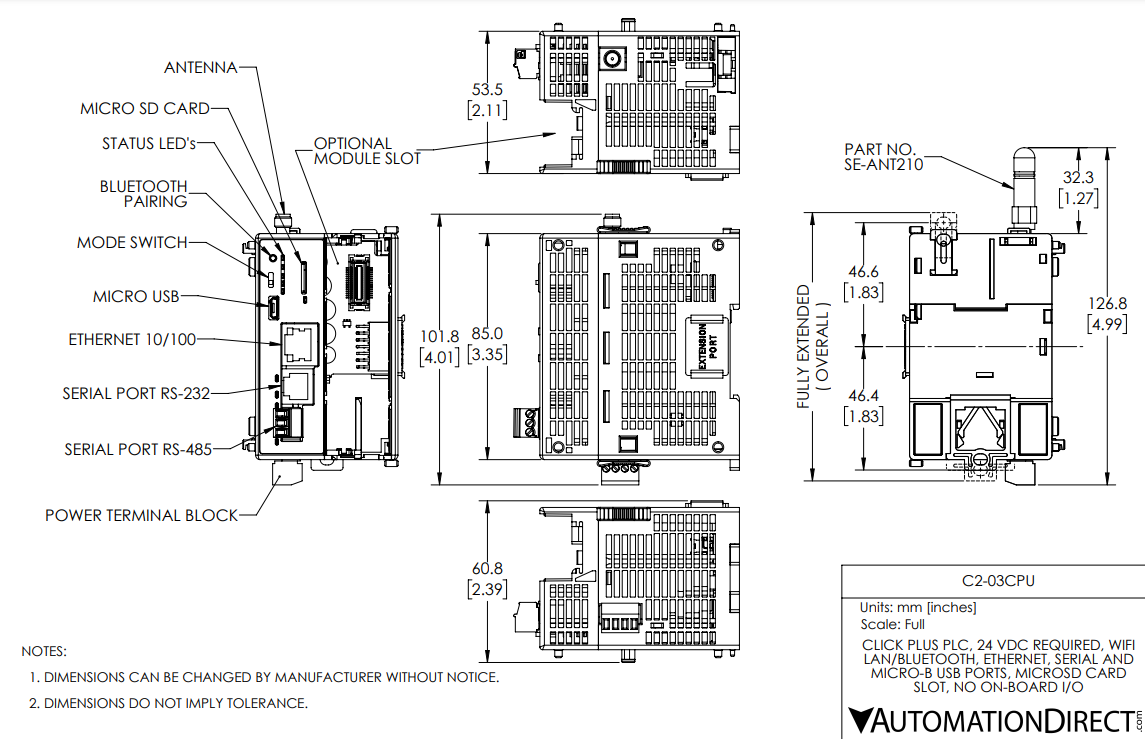
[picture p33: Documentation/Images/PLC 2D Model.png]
PLC Subsystem


*Figure 2. PLC 2D Model*

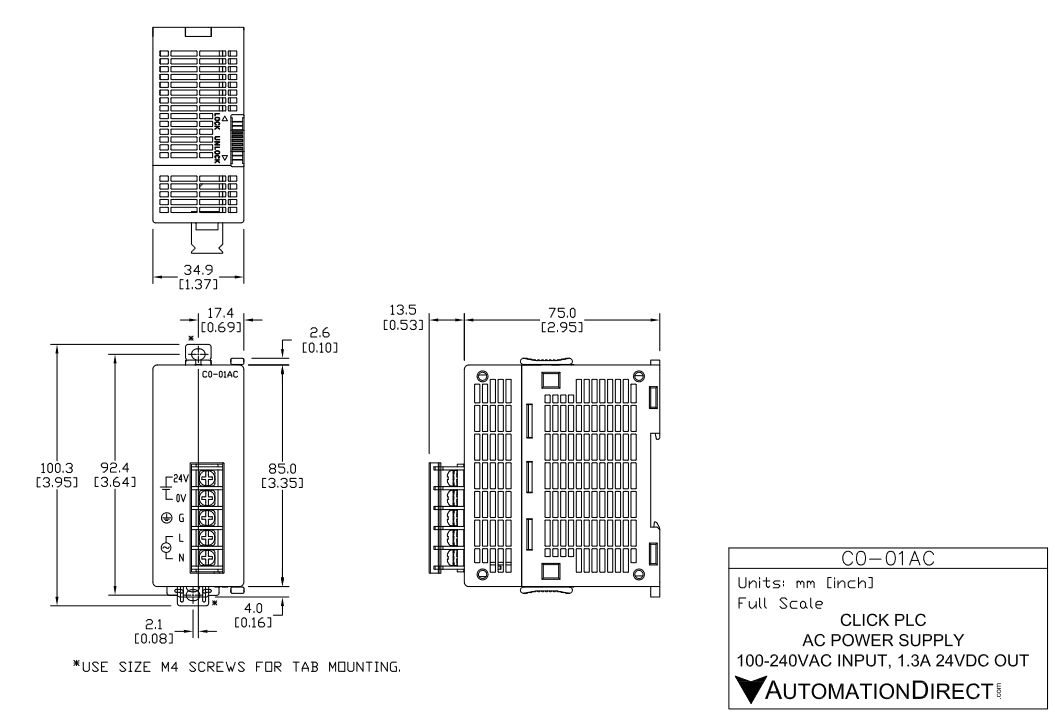
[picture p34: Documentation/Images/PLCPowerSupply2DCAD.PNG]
PLC Power Supply


*Figure 3. PLC Power Supply 2D Model*

## **Analysis:**

**PLC**
  1. The Automation Direct C2-03CPU has a scan time of < 1 ms and a contact execution of < 0.2 µs. This is more than sufficient to keep track of the sensor's data being sent every 5 minutes.
  2. The Automation Direct C2-03CPU is able to communicate through USB to USB to allow for programs to be installed. [2]
  3. The ambient humidity specifications in the PLC Datasheet show that when operating and non-condensing the relative humidity the PLC can handle is 30% to 95%. [2] This falls within our range for the greenhouse, with 80% being optimal for plant growth. [3] The PLC will also be able to monitor the humidity through communication with the Temperature/Humidity Subsystem's sensor to alert if the humidity is falling or rising to an unsafe range.
  4. In this communication setup, data collected by multiple Arduino Nano 33 IoT equipped with BLE capabilities is wirelessly transmitted to another Arduino Nano 33 IoT functioning as a gateway device. The sensor Arduinos gather data and transmit it to the gateway Arduino via Bluetooth Low Energy (BLE). Upon receiving the data, the gateway Arduino processes and formats it to align with the requirements for RS232 communication. Through a wired connection established by an RS232 cable, the gateway Arduino interfaces with the Programmable Logic Controller (PLC). It then relays the formatted data from the sensor Arduinos to the PLC via RS232, facilitating data transfer for real-time monitoring and control in the greenhouse environment. Here is example code of what it might look like to recieve/send data using this system.
```
#include <SoftwareSerial.h>
#include <ArduinoBLE.h>
#include <Ethernet.h>

#define RX_PIN 17 // RX pin of Arduino Nano 33 IoT
#define TX_PIN 16 // TX pin of Arduino Nano 33 IoT

SoftwareSerial RS232(RX_PIN, TX_PIN);

BLEService dataService("12345678-1234-5678-1234-56789abcdef0");
BLECharacteristic dataCharacteristic("0000abcd-0000-1000-8000-00805f9b34fb", BLERead | BLENotify, 20);

void setup() {
  Serial.begin(9600);
  RS232.begin(9600);
  while (!Serial);
  if (!BLE.begin()) {
    Serial.println("starting BLE failed!");
    while (1);
  }
  BLE.setLocalName("Nano33IoT");
  BLE.setAdvertisedService(dataService);
  dataService.addCharacteristic(dataCharacteristic);
  BLE.addService(dataService);
  dataCharacteristic.writeValue(0);
  BLE.advertise();
  Serial.println("BLE server is now running, waiting for connections...");
}

float parseData(String data) {
  int commaIndex = data.indexOf(',');
  if (commaIndex == -1) {
    return 0.0;
  }
  // Get the first part of the split
  String floatValue = data.substring(0, commaIndex); 
  // Convert the float value to a float and return it
  return floatValue.toFloat();
}

void sendDataToPLC(float data1, float data2, float data3, float data4) {
  String dataToSend = String(data1) + "," + String(data2) + "," + String(data3) + "," + String(data4);
  RS232.println(dataToSend);
}

float getDataFromArduino1() {
  String data = readSensorDataFromBLE();
  // Parse the data and return the value
  return parseData(data);
}

float getDataFromArduino2() {
  String data = readSensorDataFromBLE();
  // Parse the data and return the value
  return parseData(data);
}

float getDataFromArduino3() {
  String data = readSensorDataFromBLE();
  // Parse the data and return the value
  return parseData(data);
}

float getDataFromArduino4() {
  String data = readSensorDataFromBLE();
  // Parse the data and return the value
  return parseData(data);
}

void loop() {
  float data1 = getDataFromArduino1();
  float data2 = getDataFromArduino2();
  float data3 = getDataFromArduino3();
  float data4 = getDataFromArduino4();

  sendDataToPLC(data1, data2, data3, data4);
  
  delay(1000);
}
```
  5. The utilization of CLICK programming features with the PLC offers a solution for data logging requirements. By leveraging trigger bits in the ladder logic, CSV files containing data can be systematically generated and stored onto a micro SD card connected to the PLC. With a maximum file limit of 999 files and a data save interval set at every hour, calculations reveal that this setup enables the logging of data for an approximate duration of 41.625 days before reaching file capacity. This approach underscores the efficiency and reliability of the PLC subsystem, ensuring seamless data acquisition and storage over extended periods exceeding our 1 month minimum timeline. [4]
  6. In the system design the C0-01AC model power supply integrates essential protection features to ensure the safety of connected equipment. The power supply includes overcurrent protection with automatic recovery, activated at a threshold of 0.65 A, safeguarding against excessive current draw. Additionally, the system has overvoltage protection, by a Zener diode, which clamps voltage spikes at 27.6 V. These protective measures are fundamental in decreasing risks from electrical faults and keeping an uninterrupted operation from the power distribution system.
     
**Power Supply for PLC**
- The CLICK C0-01 AC will be the source used to power the PLC system, which has the ability to supply between 100-240 VAC. This supply gives a 1.3A and 25V DC source which is more than capable of supporting the PLC even with all I/O ports being used. The maximum start-up time is 1000ms, which allows plenty of time for the PLC to receive and send data to and from the other sub-systems. The humidity range allows up to 95% humidity which is ideal for the supply being used inside of a greenhouse. 
 
**HMI to PLC**
- We will use the PLC and code in "Ladder" to allow the ports to be read and sent to the HMI. The HMI then has the C-more Micro Programming Software that can be used to design and simulate the code to be used on the HMI to correctly display and customize the buttons. Here is the template to allow for communication between PLC and HMI.

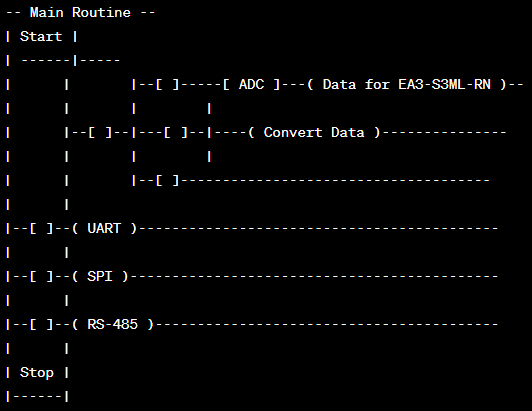
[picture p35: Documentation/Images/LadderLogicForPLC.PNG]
PLC Port Code


**Placement and Enclosure**
- Placement of the enclosure will be in the south eastern part of the building next to the greenhouse entrance and power outlet. The PLC will be enclosed in a 6.30 x 6.30 x 3.52 in weatherproof box and cable glands to allow for connection. The power supply will be enclosed in another 6.30 x 6.30 x 3.52 in enclosure with connections to the PLC and the power outlet.The cases will have 2 cable glands each to allow cables to input and output from each system.

## **Bill of Materials**
|Brand/Manufacturer|Part Name|Supplier|Part/Model Number|Quantity|Individual Price|Total|
|----|---|---|---|---|---|-----|
|CLICK PLUS|PLC|Automation Direct|C2-03CPU|1|$205.00|$205.00|
|CLICK|Power Supply|Automation Direct|C0-01AC|1|$63.00|$63.00|
|SanDisk|MicroSD|Amazon|SanDisk Ultra microSDHC 32GB|1|$7.65|$7.65|
|Polycase|Outdoor Enclosure|Ploycase|SK-18 Enclosure with Knockouts 7.09 x 5.12 x 3.31 in|1|$41.17|$41.17|
|Polycase|Cable Glands|Ploycase|CG3 Gray Cable Glands 1.53 x 1.19 x 1.19in|2|$2.86|$5.72|
|Polycase|Mounting Kit|Ploycase|SK-99 Mounting Kit for SK Series Enclosures 0.91 x 0.59 x 0.86 in|2|$3.36|$6.72|
|MAX3232|TTL to RS232 Module|Amazon|B07PFB4MHR|1|$15.99|$15.99|
|DTech|RS232 Cable|Amazon|DT-9006C 2M|1|$10.96|$10.96|
|JoinFWorld|Outdoor Enclosure|Amazon|Outdoor Electrical Box Waterproof Nema Enclosure 16x11x6 Plastic WiFi Box|1|$49.99|$49.99|

**References**

[1] AutomationDirect, "Click PLCs - CLICK PLUS Features," AutomationDirect, https://www.automationdirect.com/clickplcs/clickplus/features.

[2] AutomationDirect, "C20xCPU - CPU Module for C2000 Series PLCs," AutomationDirect, https://cdn.automationdirect.com/static/specs/c20xcpu.pdf.

[3] Atlas Scientific, "Ideal Greenhouse Temperature and Humidity," Atlas Scientific Blog, https://atlas-scientific.com/blog/ideal-greenhouse-temperature-and-humidity/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,growth%20and%20lower%20quality%20yield.

[4] AutomationDirect, "CLICK PLC Data Logging | Do-more Designer 2.0.2 Logger", AutomationDirect, https://www.automationdirect.com/videos/video?videoToPlay=rkgwh-HfNKo

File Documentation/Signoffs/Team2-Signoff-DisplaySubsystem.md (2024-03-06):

# *Detail Design: Communications Application*

## **Function of the Subsystem:**

The Display Subsystem is responsible for receiving input data from various sensors within the greenhouse, such as nutrient levels, humidity, temperature, CO2, and NO2 levels. This subsystem collects this data obtained by the Programmable Logic Controller (PLC) and relays it to the HMI (Human-Machine Interface) for display and monitoring purposes. Its primary function is to ensure the efficient handling of sensor data and present it on the HMI within the greenhouse. This subsystem serves as an intermediary, utilizing the data received and transmitting it to the visualization interface for greenhouse workers. The HMI displays real-time sensor readings, aiding in informed decision-making. Additionally, it highlights any sensors indicating measurements outside the acceptable range, providing alerts for immediate attention. The focus of this subsystem is to efficiently relay real-time sensor data in an easily understandable format on the HMI, enabling quick comprehension of the information.

## **Constraints:**

|Segment|Number|Constraint Description|
|---|-|---|
|HMI|1|The HMI shall be capable of receiving and displaying sensor data from various sources within the greenhouse, including nutrient levels, humidity, temperature, CO2, and NO2 levels.|
|HMI|2|Communication between the HMI and PLC must be robust and reliable to ensure real-time monitoring of sensor data.|
|HMI|3|The HMI shall have sufficient screen resolution and clarity to display sensor readings in an easily understandable format, including any alerts or notifications.|
|HMI|4|Power supply for the HMI shall provide stable wattage at 1.05W to ensure uninterrupted operation of the display system.|

## **Buildable Schematic:**

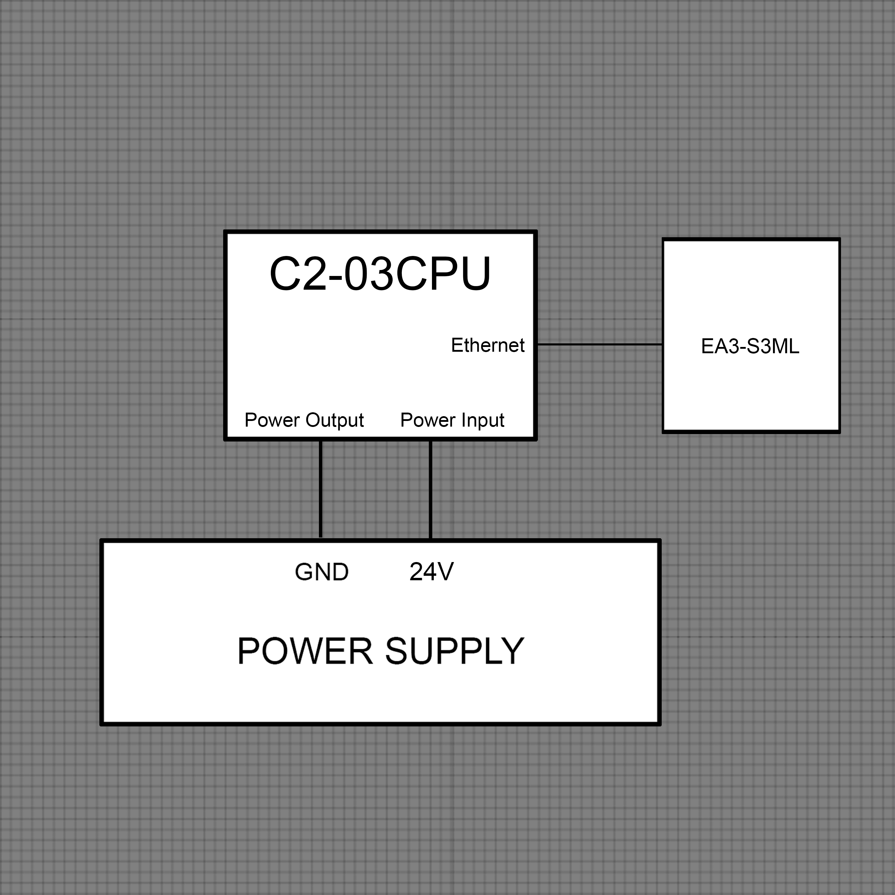
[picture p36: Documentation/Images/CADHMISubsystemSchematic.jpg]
HMI Design


*Figure 1. HMI Subsystem Design*

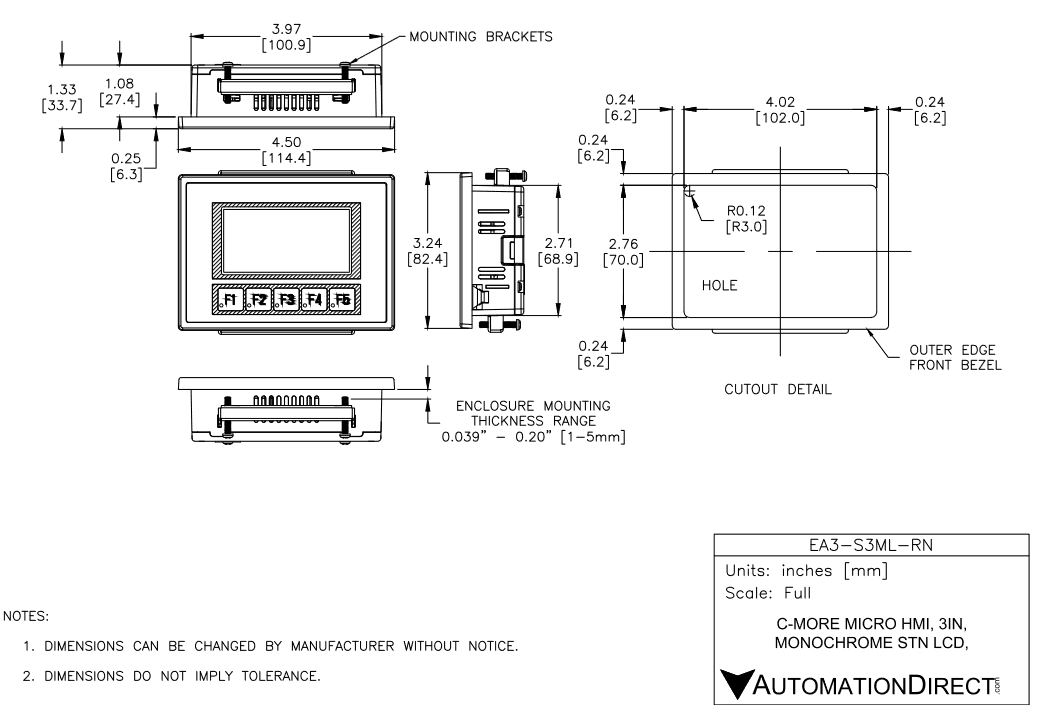
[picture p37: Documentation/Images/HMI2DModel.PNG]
HMI 2D Model


*Figure 2. HMI 2D Model*

## **Analysis:**

**HMI**
1. **Capability to Display Sensor Data**: The EA3-S3ML HMI is specifically designed to receive and display sensor data from various sources from the C2-03CPU PLC. With its customizable graphical interface and support for multiple data formats, including integers from the PLC, it ensures that all sensor readings are accurately presented to greenhouse workers in real-time. [1]

2. **Robust Communication with PLC**: The communication between the HMI and PLC will be established via ethernet cable connections, ensuring a robust and reliable data link. By using dedicated ethernet ports on both the HMI and PLC, we will see seamless communication, meeting the requirements for real-time monitoring of sensor data. [1]

3. **Screen Resolution and Clarity**: The HMI boasts a display with 128 x 64 pixel resolution, allowing for the easy visualization of sensor readings, alerts, and notifications. Through the C-more Micro Programming Software, the graphical elements on the HMI can be customized to ensure that all information is presented in a clear and understandable format, meeting the demands for effective decision-making. This HMI is capable of allowing up to 999 screens each with different customization options for the buttons. It has 10 lines by 32 characters to be used to ensure clarity. [1]

4. **Stable Power Supply**: To ensure uninterrupted operation, the HMI will be powered by a stable power supply at 1.05W provided by the ethernet port on the PLC. [1]

**HMI Mounting**

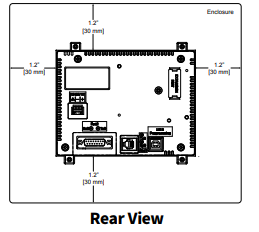
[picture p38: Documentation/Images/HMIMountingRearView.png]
HMI Mounting Rear


*Figure 3. HMI Mounting Rear View*

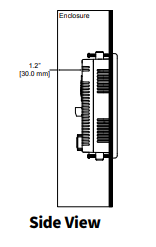
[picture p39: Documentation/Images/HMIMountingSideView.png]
HMI Mounting Side


*Figure 4. HMI Mounting Side View*

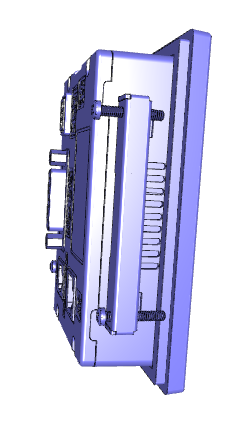
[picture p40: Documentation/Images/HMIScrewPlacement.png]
3D HMI with Bracket


*Figure 5. HMI 3D Schematic with Bracket*

The PLC will sit in a 16 x 11 x 5.5 inch enclosure. This is more than enough for the HMI as it needs 4.5 inches for the width plus an additional 1.2 inch on each side. [1] Thus, the 11 inch enclosure will allow us to make a 3.26 x 4.5 inch cutout in the 16 x 11 inch enclosure face and meet the requirements of having at least a 6.9 inch width enclosure. We will then use the mounting bracket and tighten the screws the the enclosure from the inside. You can see on the 3D schematic above, the screws will be tightened from the inside of the case and make contact to secure the HMI in the cutout. 

## **Bill of Materials**
|Brand/Manufacturer|Part Name|Supplier|Part/Model Number|Quantity|Individual Price|Total|
|----|---|---|---|---|---|-----|
|C-more Micro|HMI|Automation Direct|EA3-S3ML|1|$280.00|$280.00|
|Automation Direct|Ethernet Cable|Automation Direct|C5E-STPBL-S3|1|$6.75|$6.75|

**References**

[1] AutomationDirect, "C-more Micro Operator Interface Panels," AutomationDirect, https://www.automationdirect.com/c-moremicro/ea3-series.

[2] M. Margolis and M. Fisher, "Chapter 4: Sensing the World," O'Reilly Media, 2011. [Online]. Available: 
<https://www.oreilly.com/library/view/arduino-cookbook/9781449399368/ch04.html> 
Accessed on: October 31, 2023.

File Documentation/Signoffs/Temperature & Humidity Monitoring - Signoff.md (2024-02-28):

# *Detail Design: Temperature and Humidity Control*
## **Team 2 - Greenhouse Project**
### *Team Members: Jared Hooker and Noah Jones*

## **Function of the Subsystem:**
The function of this subsystem is to measure the temperature and the humidity levels in the greenhouse. The DHT20 sensor will measure both values, then relay the information to the Arduino Nano 33 IoT device. 

## **Constraints:**

- **Arduino Nano 33 IoT**
  1. The communication between the Arduino and the PLC must be wireless. This will allow for the system to be scalable, meaning that the greenhouse can be expanded to add more zones if needed.
  2. The data transfer from the sensors to the Arduino must be below 5 seconds to allow an adequate amount of time before the Arduino returns to its sleep mode.
  3. The Arduino shall be able to wirelessly transmit the data to the gateway Arduino Nano 33 IoT and PLC in a cost effective way.

- **DHT20 Temperature & Humidity Sensor**
  1. The sensor shall have 2.5-5.5 V to operate correctly.
  2. Sensor uses 3.2mW when on, and 0 W when in sleep mode.
  3. Temperature range of 0-50°C (32-122°F) and humidity range of 20-90%.
  4. Sampling period of greater than or equal to 2 seconds, so it is set to be 10 seconds to allow for extra time.

## **Buildable Schematic:**
Buildable Schematic Temperature & Humidity Monitoring
## **Analysis:**
- **Arduino Nano 33 IoT**
  1. The power supply will be four AA batteries. Each battery contains 1.1-1.5 volts, which will give the Arduino the required 5 volts.
  2. The Arduino will turn on for 10 seconds once every 5 minutes. This can be done using functions from the Arduino-Libraries Github [1]. By instructing the Arduino to go into sleep mode using the LowPower.sleep() function, the desired time range can be achieved.
  3. Using Bluetooth Low Energy (BLE) allows for a cost efficient manner to transmit data throughout the greenhouse. A disadvantage of BLE is the decreased distance that information can be transmitted. Most BLE devices can trasmit/receive data at a max rate of 50 meters [2]. However, the distance between the Arduino and the PLC will only be 15 feet, or 4.57 meters.
 
- **DHT20 Temperature & Humidity Sensor**
    1. The DHT20 temperature and humidity sensor is powered by the Arduino. An output voltage of 5 V is sent to the DHT20 via the Arduino.
    2. The DHT20 does not consume much power from the batteries. The amount of power from the DHT20 and Arduino are as follows:
       - AA batteries supply 1.5V and 3500mAh each. P = (1.5V*3500mAh) * 4 batteries = 21Wh
       - Arduino uses 5V and 28mA while in the "on" mode. P = (5V * 28mA) * (120s/3600s) = 4.67mWh.
       - Sensor uses 3.2mW while on, and 0.8μW in the "dormant" state. P = (3.2mW) * (120s/3600s) + (0.8μW) * (3480s/3600s) = 0.107mWh
       - Total power consumed: P = 4.67mWh + 0.107mWh = 4.777mWh. 21Wh/4.777mWh = 4,396.1 hours or 6.11 months.
    3. The temperature and humidity ranges are ideal for greenhouses. When speaking to the greenhouse coordinator, the temperature ranges from 60-85°, and humidity ranges from 50-80% in this specific greenhouse. The goal for this subsystem is to send an alert to the PLC to notify the manager when the temperature or humidity is out of these specific ranges. 
    4. The DHT20 must be on for at least 2 seconds in order to detect the temperature and humidity, as well as send the data to the Arduino. By leaving the Arduino on for 10 seconds, the sensor will have a sufficient amount of time to measure and transmit the data. Once the data is retrieved from the MCU, the sensor automatically goes back into the "dormant" mode. It will stay in this mode until it recieves a start up signal from the MCU to measure the temperature and humidity values again. [3]
    5. The sensor will communicate via I2C using SDA and SCL lines. The datasheet mentions that there are two SDA lines, one controlled by the sensor and the other by the MCU, which is the Arduino Nano 33 IoT. During communication, both the sensor and the MCU will have control over the SDA line at different times, depending on the direction of communication. The start and stop transmission states in the I2C protocol are as following. When initiating a transmission sequence, the Arduino will generate the start condition by pulling the SDA line low while SCL is high. This signals the beginning of a communication session. Similarly, the stop condition is generated by the Arduino by releasing the SDA line, allowing it to go high while SCL is high, indicating the end of communication. For the timing of the SCL and SDA, the falling edge of SCL will trigger the SDA to read. This means that data on the SDA line should be stable and valid by the time the falling edge of SCL occurs, indicating a point in time when the data can be read. Overall, SDA and SCL work together in the I2C protocol to facilitate communication between the sensor and the Arduino. SCL provides the clock signal that synchronizes data transfer, while SDA carries the actual data being transmitted or received. [3]

 - **Communication for DHT20**
     1. The DHT20 follows inter-integrated circuit (I2C) protocol to communicate with the Arduino 33 IoT. I2C is supported on all Arduino boards. [4]
    
## **Bill of Materials:**
|Brand/Manufacturer|Part Name|Supplier|Part/Model Number|Quantity|Individual Price|Total|
|----|---|---|---|---|---|-----|
|Adafruit|Temperature and Humidity Sensor|Adafruit|DHT20|2|$4.50|$9.00|
|Arduino|Bluetooth Board|Arduino|Nano 33 IOT|1|$26.30|$26.30|
|LAMPVPATH|4 AA Battery Holder|Amazon|B07L9M6VZK|1|$7.49|$7.49|
|Duracell|AA Batteries|Amazon|DURMN1500B10Z|1|$8.79|$8.79|

## **References:**
[1]  “Arduino Low Power - Arduino Reference,” www.arduino.cc, Nov. 08, 2023). ‌https://www.arduino.cc/reference/en/libraries/arduino-low-power/

[2] “Advantages of BLE (Bluetooth Low Energy) | disadvantages of BLE (Bluetooth Low Energy),” www.rfwireless-world.com. https://www.rfwireless-world.com/Terminology/Advantages-and-Disadvantages-of-BLE-Bluetooth-Low-Energy.html

[3] SparkFun Electronics, "DHT20 Sensor Datasheet," SparkFun Electronics, https://cdn.sparkfun.com/assets/8/a/1/5/0/DHT20.pdf

[4] Arduino.cc, 2024. https://docs.arduino.cc/learn/communication/wire/

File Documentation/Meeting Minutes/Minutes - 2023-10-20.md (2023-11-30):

 

# Meeting Minutes – Greenhouse Project #

**Location:**

**Date:**

Online

Friday, October 20th

1:30 PM

**Time:**

**Attendance**

Noah Jones

Jared Hooker

Grant Hooper

Bryan Rhoton

Jaxson Billings

EOSYS

**Agenda Items**

1\. Project Proposal Review

2\. Conceptual Design & Planning Review

**Action Items**

1\. Keep Visualization Screen separate from the logic and control system. Don’t have them

interlocked.

2\. Consider other systems besides Arduinos because of longevity.

3\. Remote I/O modules. They live away from the PLC and communicates through ethernet or other

network calls instead of Arduinos.

4\. Research RS485 Serial.

5\. Research Automation Direct.

6\. Make sure sensors and parts used are going to be compatible with our PLC Controller.

7\. Greenhouse Layout

8\. PNIV / Process Flow Diagram

**Individual Items**

Noah Jones: Digital Design for Temperature/Humidity & Light Controller

Jared Hooker: Digital Design for PLC Controller & Temperature/Humidity

Grant Hooper: Digital Design for PLC Controller & Light Controller

Page 2 of 2

Bryan Rhoton: Digital Design for Communications Application & Nutrient Subsystem

Jaxson Billings: Digital Design for Communications Application & Nutrient Subsystem. Meeting minutes

for EOSYS Meeting

Group: Digital Design for CO<sub>2</sub> Subsystem

**Other Notes**

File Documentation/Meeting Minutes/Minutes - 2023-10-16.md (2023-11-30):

 

Meeting Minutes – Greenhouse Project*

**Location:**

**Date:**

Brown Hall Room 408

Monday, October 16th

4:30 PM

**Time:**

**Attendance**

Noah Jones

Jared Hooker

Grant Hooper

Bryan Rhoton

Jaxson Billings

**Agenda Items**

1\. Conceptual Design with EOSYS

2\. Digital Design Planning

3\. Consult Supervisor & Sponsor

4\. Talk about first subsystem in Digital Design

**Action Items**

1\. Got contacts for Hyder-Burks Greenhouse

2\. Made a list of subsystems needed for Digital Design

a. Temperature & Humidity - wirelessly

b. Water & Nutrient Control - wirelessly

c. CO<sub>2</sub> & Nitrogen - wirelessly

d. Communications/Application/Trends

e. Colors/Lighting

f. PLC Controller

3\. Decided for Digital Design to start with peripherals and end with PLC Controller

4\. Plan for Conceptual Design Revision (don’t turn in)

5\. Start CO<sub>2</sub> & Nitrogen Subsystem Digital Design

6\. Checkpoint 1 & 2 (October 25 & November 1, Respectively)

7\. Survey due October 17th

**Individual Items**

Page 2 of 2

Noah Jones: Digital Design for Temperature/Humidity & Light Controller

Jared Hooker: Digital Design for PLC Controller & Temperature/Humidity

Grant Hooper: Digital Design for PLC Controller & Light Controller

Bryan Rhoton: Digital Design for Communications Application & Nutrient Subsystem

Jaxson Billings: Digital Design for Communications Application & Nutrient Subsystem. Meeting minutes

for the week, due 10/16/23

Group: Digital Design for CO<sub>2</sub> Subsystem

**Other Notes**

Research for Carbon Dioxide control.

Everything Wireless.

Think more about scalability.

Use current irrigation system to fill up a local reservoir which can then be used for a manual override for

watering (use zones).

Automation Direct (PLC Controller).

Box around PLC.

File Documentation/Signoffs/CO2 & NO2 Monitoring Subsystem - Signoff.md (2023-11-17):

 

# *Detail Design: CO2 and NO2 Sensor*

## **Function of the Subsystem:**

  The function of this subsystem is to relay the CO<sub>2</sub> and NO<sub>2</sub> levels to the Arduino via their respective sensors. The subsystem will use a series of sensors to transfer the percentage levels of CO<sub>2</sub> and NO<sub>2</sub> in the air to the Arduino. The sensors will monitor the changes of the carbon dioxide and nitrogen dioxide levels in the greenhouse’s atmosphere and will report these numbers and changes to the Arduino.

## **Constraints:**

- **Carbon Dioxide Sensor – MH-Z19B**
  1. MH-Z19B needs between 4.5-5.5V and at least 20mA to operate eﬃciently.
  2. The sensor must turn on every 5 minutes to measure the amount of carbon dioxide present in the greenhouse.
  3. Must alert the communications applications when above or below 400-2000ppm to ensure proper plant growth. [1]

- **Arduino Nano 33 IoT**
  1. The communication between the sensors and PLC must be wireless. This will save time and money on wiring, while also allowing the system to be scalable, meaning if the greenhouse was to be expanded then this subsystem would be easily expanded to account for more plants.
  2. The transfer of data between the sensors and the Arduino must be below 3 seconds for accurate and reliable monitoring of the CO<sub>2</sub> and NO<sub>2</sub> levels in the atmosphere and to allow plenty of time for communication with the PLC while looping in and out of sleep mode.
  3. The system needs to be capable of wirelessly communicating the collected data back to the PLC in an inexpensive, yet reliable way.

- **Nitrogen Dioxide Sensor – MIKROE-3700**
  1. MIKROE-3700 needs between 3.3-5V to operate efficiently.
  2. Must alert when above Nitrogen Dioxide level exceeds 9 ppb. [2]

## **Buildable Schematic:**

Buildable Schematic CO2 and NO2

*Figure 1. Wiring Schematic for Power to Sensors*

Arduino Nano 33

*Figure 2. Arduino Nano 33 IoT Board Topology*

## **Analysis:**

- **Carbon Dioxide Sensor – MH-Z19B**
  1. The sensor will be supplied 5V from the AA battery pack.
  2. It will turn on for 10 seconds every 5 minutes, this gives the system enough time to send the data to the PLC.
  3. The sensor will be set with the detection range option of 400-2000ppm and will send alerts if carbon dioxide concentrations fall above or below that range.
     
  - **Power Supply for MH-Z19B**
    - The MH-Z19B will use Pin 4 connected to the Nano 33 IoT’s Pin 12 supplying 5 volts to the sensor.
    - MH-Z19B’s Pin 3 will be used as its ground and shall be connected to the Nano 33 IoT’s Pin 19, completing the power circuit, and powering the sensor.
    - The working voltage will be 4.5 ~ 5.5 V DC
    - Average Current < 20mA with a 5V power supply
    - Response Time of T<sub>90</sub> < 120 s
    - Working Humidity of 0 ~ 95% RH (No condensation)
    - The average current draw is 20mA
    - Therefore, the energy used during the "while on" mode is (20mA x 5V) x (10s / 3600s) = .028mWh
    - The average power drawn is .028 / (5min / 60min) = .33mW

  - **Communication for MH-Z19B**
    - MH-Z19B will use Pin 5 for UART (Rx) TTL Level data input which will be connected to the Nano 33 IoT’s Pin 17 which is used as an USART Digital Rx
    - MH-Z19B will use Pin 6 for UART (Tx) TTL Level data input which will be connected to the Nano 33 IoT’s Pin 16 which is used as an USART Digital Tx
    - The Carbon Dioxide detection range consists of options 400-2000ppm, 400-5000ppm, or 400-10,000ppm. It has an accuracy of ±(50ppm+5% reading value)
    - PWM Output consists of the following:
      - Cycle of 1004ms±5%
      - Cycle start high level output of 2ms, theoretically.
      - Middle Cycle of 1000ms±5%
      - Cycle end high level output of 2ms, theoretically.

  PWM Graph

- **Arduino Nano 33 IoT**
  1. The Arduino's BLE capabilities could be broadened by using an array of bluetooth extenders if required for larger projects.
  2. The Ardiuno will need to be cycled in and out of sleep mode to conserve battery life. This will be done by using the Arduino-Libraries Github and use the provided files and functions in the ArduinoLowPower folder. For example, we can use the function LowPower.sleep() and input the amount of time we want it to sleep in ms. Implementing this in a loop will then allow the microcontroller to continuously fall asleep and wake up for the desired time. We have decided to do a system where the Ardiuno runs for 10 seconds for every 5 minutes. [3]
  3. BLE (Bluetooth Low Energy) is lower in cost than the classic Bluetooth as BLE is currently rising in use and has market competition. BLE decreases the distance a signal can be transmitted, but the signals transmitted through the greenhouse will not be far apart. The use of BLE allows for a cost-eﬃcient alternative compared to standard Bluetooth.

  - **Power Supply for Arduino Nano 33 IoT**
    - The power used will need to supply 5 volts to the Pin 15 on the Nano 33 IoT.
    - The Pin 14 on the Nano 33 IoT will need to be connected to the ground from the power supply.
    - The Arduino will be powered by 4 AA batteries which supplies 3500mAh and 1.5V each
    - The total mWh supplied is equal to (1.5V x 4) x 3500 = 21,000mWh
    - Therefore, the energy used during the "while on" mode is (28mA x 5V) x (10s / 3600s) = .07778mWh
    - The average power is .07778 / (5min / 60min) = 0.933mW
    - The total power used by both sensors and the Arduino is .933mW + .33mW + .0828mW = 1.346mW
    - This means the batteries will last (21,000mWh / 1.346mW) = 15,601 hours or 21.7 months

- **CO<sub>2</sub> and NO<sub>2</sub> Levels**
    - The average concentration of CO<sub>2</sub> found in the atmosphere is around 400 parts per million (ppm), but greenhouses often produce greater concentrations. This is due to a greater plant yield at higher levels. If the level of CO<sub>2</sub> in the greenhouse is between 400-2000 ppm, the plants are able to have a greater increase in growth. However, any ranges outside of these parameters result in a negative growth rate for the plants. [4]
    - According to the CDC, anything over 5ppm is considered dangerous for an extended period of time. [2]

- **MIKROE-3700**
  1. The sensor will receive an input voltage of 3.3V from the Arduino's output pin which is within the sensor's operating voltage range.
  2. In order to use the 12-bit ADC, which is the output of the sensor, a reference voltage of 3.3V will need to be used for calibration. We can use the following equation, V = ( D / 2^12 -1) x Vref. This is the analog voltage to digital value formula to compute that a digital value of .009 will be approximately 7.62mV. This signal will alert the Arduino of unsafe Nitrogen Dioxide levels. 
     
  - **Power Supply for MIKROE-3700**
    - The MIKROE-3700 will use Pin 10 connected to the Nano 33 IoT’s Pin 2 as a 3.3V power supply. This will run through a 10k ohm and 20k ohm voltage divider to ensure the voltage level is brought down.
    - MIKROE-3700’s Pin 8 will be connected to the Nano 33 IoT’s Pin 19 as a ground to complete the power circuit and be able to supply the 3.3V needed.
    - The measurement range has a minimum of 0ppm and a maximum of 10ppm.
    - The response time is 200s.
    - Operating Humidity Range is 5 ~ 95% RH (No condensation).
    - The time the sensor will be on is 10 seconds every 5 minutes
    - The average current draw is .5mA
    - Therefore, the energy used during the "while on" mode is (.5mA x 5V) x (10s / 3600s) = .0069mWh
    - The average power is .0069 / (5min / 60min) = .0828mW

  - **Communication for MIKROE-3700**
    - The MIKROE-3700’s Pin 5 will be used as a SPI Data Out connected to the Nano 33 IoT’s Pin 30 which is used as a Digital SPI MISO.
    - The MIKROE-3700’s Pin 4 will be used as a SPI Clock connected to the Nano 33 IoT’s Pin 11 which is used as a signal sent to mimic a clock and when to grab the data.
   
- **Silicon Conformal Coating**
  - Service temperature range of -40-200℃
  - Resistivity of 3.5 x 1013 Ω·cm
  - Drying time of 15 minutes for 2 coats
  - Will be used to keep electrical components safe from water

## **Bill of Materials**
|Brand/Manufacturer|Part Name|Supplier|Part/Model Number|Quantity|Individual Price|Total|
|----|---|---|---|---|---|-----|
|MikroElektronika|NO2 Sensor|DigiKey|1471-MIKROE-3700-ND|1|$39.00|$39.00|
|MiZOELEC|CO2 Sensor|Amazon|MH-Z19B|1|$35.00|$35.00|
|Arduino|Bluetooth Board|Arduino|Nano 33 IoT|1|$25.50|$25.50|
|MG Chemicals|Silicon Conformal Coating|DigiKey|422C-55MLCA|1|$23.94|$23.94|
|LAMPVPATH|4 AA Battery Holder|Amazon|B07L9M6VZK|1|$7.49|$7.49|
|Duracell|AA Batteries|Amazon|DURMN1500B10Z|1|$8.79|$8.79|

**References**

[1]“Supplemental carbon dioxide in greenhouses | ontario.ca,” www.ontario.ca. https://www.ontario.ca/page/supplemental-carbon-dioxide-greenhouses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 (accessed Nov. 09, 2023).
‌

[2] Q. Sheng and Z. Zhu, “Effects of Nitrogen Dioxide on Biochemical Responses in 41 Garden Plants,” Plants, vol. 8, no. 2, p. 45, Feb. 2019, doi: https://doi.org/10.3390/plants8020045.
‌

[3] “Arduino Low Power - Arduino Reference,” www.arduino.cc, Nov. 08, 2023).
‌<https://www.arduino.cc/reference/en/libraries/arduino-low-power/>

[4] “Greenhouse Carbon Dioxide Supplementation - Oklahoma State University,” extension.okstate.edu. 
<https://extension.okstate.edu/fact-sheets/greenhouse-carbon-dioxide-supplementation.html>

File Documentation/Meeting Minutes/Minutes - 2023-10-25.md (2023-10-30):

 

Page 1 of 2

Meeting Minutes – Greenhouse Project

**Location:**

**Date:**

Online

Friday, October 20th

1:30 PM

**Time:**

**Attendance**

Noah Jones

Jared Hooker

Grant Hooper

Bryan Rhoton

Jaxson Billings

EOSYS

**Agenda Items**

1\. CO2 & NO2 Design Signoff

**Action Items**

1\. Establish Better Constraints.

2\. Add labels to Buildable Schematic.

3\. Build a system based off what is needed.

4\. Use 555 to possibly tell when Arduino needs to turn on and grab/enable the sensors to receive

and send data (saves data).

5\. Nyquist rate (fastest time concentration of air can change divided by 2)

6\. Sleep Mode on Arduino?

7\. Enable/Disable on Sensors?

8\. Current Drawn On vs Off.

9\. Look at other sensors/projects and how they last for long periods of time.

**Individual Items**

Noah Jones: Digital Design for Temperature/Humidity & Light Controller

Jared Hooker: Digital Design for PLC Controller & Temperature/Humidity

Grant Hooper: Digital Design for PLC Controller & Light Controller

Bryan Rhoton: Digital Design for Communications Application & Nutrient Subsystem

Page 2 of 2

Jaxson Billings: Digital Design for Communications Application & Nutrient Subsystem. Meeting minutes

for Jesse Meeting

Group: Digital Design for CO<sub>2</sub> Subsystem

**Other Notes**

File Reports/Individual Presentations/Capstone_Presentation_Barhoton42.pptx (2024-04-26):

## Voltage Regulators

By: Bryan Rhoton

## Intro

- Voltage Regulators, also known as voltage converters, are a group of electronic components designed to provide a constant voltage output with a varying voltage input.
- There are two main types of these regulators: switching and linear.
- The main difference between the two types is the difference in the efficiencies in their outputs [1].

Figure 1. Linear and Switching Regulator Circuits
Source: adapted from [2]

Linear Voltage Regulator vs. Switching Regulator - Integrated Circuits (ICs) - Electronic Component and Engineering Solution Forum - TechForum │ DigiKey

## Types

- There are several different types of switching regulators including:
  - Step-up regulators
  - Step-down regulators
  - Inverting regulators
  - Step-up / Step-down regulators


Figure 2. Buck-boost Converter
Source: Adapted from [3]

## What They Do

- Switching regulators are used to convert only dc voltages specifically, they are also regularly referred to as dc-to-dc converters.
- Step up/down regulators, also called buck/boost converters, specifically are used to convert input voltages to either higher or lower voltages depending on the desired output.

## How They Work (1)

- Buck-boost converters use two separate modes to control if the converter is “bucking” or “boosting”.
- While in “buck” mode the converter will produce a lower voltage than the input and while in “boost” mode it will produce a higher voltage.
- They usually operate by using a transistor as a switch connected to a diode to control current flow through an inductor and a capacitor with energy being stored with the inductor in the “on” state and dispersed to the output via the diode in the “off” state.
- The converter’s output voltage is controlled via the switch’s duty cycle which allows the converter to maintain a desired voltage level for prolonged periods [3].

## How They Work (2)

- When the switch is set in the “on” position the input voltage is connected directly to the inductor causing its current to rise in a linear fashion until reaching its maximum value.
- When in the “off” position, the inductor current is passed through the diode to supply the desired voltage to the load over time the current inside the inductor is reduced to its minimum value resetting the cycle.
- While in the resting state there is no voltage across the inductor [3].

## Voltage Supply Calculations

- The following are some examples of calculations for the supplied voltages:
- Positive switch voltage = power supply voltage x time on
- Negative switch voltage = load voltage x time off

## Regulator Modes

- Buck-boost converters have two distinct modes that they operate in indicated by the behavior of the inductor’s current during the switching cycle:
  - Continuous Conduction Mode or CCM, current never reaches zero and is always positive.
    - Advantages: Better responsiveness and efficiency
    - Disadvantages: Larger inductor values
  - Discontinuous Conduction Mod or DCM, current periodically reaches zero.
    - Advantages: Smaller inductor values and more compact design
    - Disadvantages: Bigger output ripple and less efficiency
- Some converters operate in both modes switching between the two when necessary [3].

## Mode Uses

- CCM is frequently used in large power applications due to its highly reliable output and responsiveness.
- CCM is also used when output voltage needs to remain relatively constant and cannot be widely varied.
- DCM is typically used in low power applications and situations with extremely low load current due to its lower efficiency and higher output ripple voltage [3].

## Design Process (1)

- When designing a buck-boost converter one must consider several factors including:
  - Selection of components
  - Strategy by which to control components
  - Calculations for required parameters
  - Capacitor capacitances
- Component considerations:
  - Appropriate voltage and current ratings for switches
  - Low forward voltage drop and quick recovery time for diodes
  - Maintainability of chosen conduction mode for inductors
  - Low series resistance and high capacitance for capacitors [3]

## Design Process (2)

- Control strategy considerations:
  - Desired output voltage, usually managed with pulse-width modulation (PWM)
  - Circuit stability
- Parameter considerations:
  - Duty cycle, to control output voltage
  - Inductance, to determine conduction mode ripple of output voltage [3]

## Typical Essential Components

- Buck-boost converters usually consist of the following components:
  - A switch, or switching device, which is usually a transistor chosen to regulate the inductor’s current flow and to determine the converters modes of operation and voltage output.
  - A diode to direct current from the inductor to the load and to prevent the capacitor from outputting voltage to the input.
  - An inductor to store energy and disperse it to the load depending on the switch’s “on/off” cycle.
  - A capacitor to provide a smooth and stable output voltage.
  - And finally input and output filters to reduce interference and “noise” from outside sources [3].

## Design Parameter Equations

- Duty Cycle = Output Voltage / (Input Voltage + Output Voltage)
- Output Voltage = Input Voltage x (Time On / Time Off)
- Inductor Value = (Input Voltage x Duty Cycle) / (Change in Inductor Current over Time x Switch Frequency)

## Regulator Efficiency and Circuit Losses (1)

- The overall efficiency of a buck-boost converter circuit is dependent on several factors including:
  - Losses in conduction
  - Efficiency of the switch
  - Losses due to magnetic energy
  - Control circuitry based losses
- Losses in circuit conduction causes:
  - Individual component’s natural resistances
  - Current through the switch and its “on” mode resistance
  - Current through the diode and its forward voltage drop [3]

## Regulator Efficiency and Circuit Losses (2)

- Switching efficiency is affected by the time it takes for the chosen device to switch from its “on” state into its “off” state and vice versa.
- Magnetic energy loss causes:
  - Inductor core material
  - Wire winding method
- The chosen wiring and circuitry for the converter’s controls cause minimal losses within power efficiency but are still considered when calculating the overall converter efficiency [3].

## Advantages

- Energy efficient
- Fewer external components
- Smaller components
- Availability of both step-up and step-down voltages
- Cost efficient [4]

## Disadvantages

- High gains not possible
- No input/output isolation [4]


Figure 4. Buck-boost Converter Example
Source: Adapted from [5]

## Uses

- Portable and handheld devices
- Energy collection and storage systems
- Vehicles
- Industrial and communication technology
- Lighting [3]


Figure 5. Converter Inside Electric Vehicle
Source: Adapted from [6]

## References

- [1] Monolithic Power Systems. “Voltage Regulator Types and Working Principles”. (2024). Accessed: Mar. 20, 2024. [online]. Available: https://www.monolithicpower.com/en/voltage-regulator-types#:~:text=There%20are%20two%20main%20types,regulators%20operate%20with%20high%20efficiency.
- [2] DigiKey. “Linear Voltage Regulator vs. Switching Regulator”. (Nov. 2017). Accessed: Mar. 21, 2024. [online]. Available: https://forum.digikey.com/t/linear-voltage-regulator-vs-switching-regulator/817
- [3] Monolithic Power Systems. “Buck-Boost Converters”. (2024). Accessed: Mar. 20, 2024. [online]. Available: https://www.monolithicpower.com/en/power-electronics/dc-dc-converters/buck-boost-converters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,the%20output%20through%20the%20diode.
- [4] L. James, “Advantages of buck-boost converters”. Power & Beyond. Accessed: Mar. 20, 2024. [online]. Available: https://www.power-and-beyond.com/advantages-of-buck-boost-converters-a-f75372c245154eb05a436628cb0a8faa/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,–%20no%20in-between).
- [5] Ebay. Accessed: Mar. 21, 2024. [online]. Available: https://www.ebay.com/itm/225508000268
- [6] C. Gonzalez-Castano, C. Restrepo, S. Kouro, E. Vidal-Idiarte, J. Calvente, “A Bidirectional Versatile Buck-Boost Converter Driver for Electric Vehicle Applications,” Sensors, vol. 21, no. 17, Aug. 2024. Accessed: Mar. 21, 2024. doi: 10.3390/s21175712 (https://doi.org/10.3390/s21175712). [online]. Available: https://www.mdpi.com/1424-8220/21/17/5712.

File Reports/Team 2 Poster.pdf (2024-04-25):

# Greenhouse Automation

### Robert Jones Jaxson Billings Jared Hooker Bryan Rhoton Grant Hooper

# Project Overview


From left, Grant, Jared, Robert, Jaxson, and Bryan

Degrees Farenheit; Attempt Number; Measured vs Set Temperature; Set; Measured

The overall objective of this project is to address the issue of automation inside of a greenhouse using a PLC System.

In addition to the PLC System the designed components are capable of monitoring the water level supply, measuring the temperature, humidity, CO2 and NO2 levels, nutrient levels within the soil, and also provide additional lighting for growth. These measurements are visible to the user on an HMI (Human Machine Interface) for easy view of the system. The HMI also allows the user to change the interval of time that the light are in use.


# Specifications

- All communication must be done wirelessly and sent within 5 seconds to conserve power
- Components must be durable to withstand the conditions present inside the greenhouse
- All sensors must send new data every 3 minutes to ensure accurate readings are visible on the HMI
- All data must be logged and kept for a minimum of one month
- Systems must be scalable to allow for future work


# Acknowledgements

# Design

- Lighting – Composed of four high intensity grow lights which are powered through a breaker and relay. The relay allows an Arduino to turn the lights on and off.
- CO2 and NO2 – Allows monitoring of levels within the house and report them to the user via the HMI.
- Temperature and Humidity – Allows monitoring of levels in real-time and then reports to the user to allow them to make adjustments as needed.
- Water Level – The sensor will be placed in the house’s water supply to alert the user when it is low and needs to be replenished
- Nutrients – Gives readings from the soil of each plant in the system to show which nutrients the plant is lacking or has a surplus of.
- PLC – Takes in all data from each system, stores it, and then converts the data to readable form and sends it to the HMI.
- HMI – The Human Machine Interface allows the user to check the levels of each system via touchscreen. It also allows for adjustments to be made to the lighting on/off cycle.

Our team would like to provide a special thank you to our sponsor, EOSYS, the mechanical engineering and agricultural departments, Mr. Jesse Roberts, Dr. Jeffrey Austen, Mr. Conard Murray, Mr. James Baier, and our advisor Mr. Jeremy Bastoky from EOSYS.

# Experimentation and Results

Shown in the graph above are the experimental results from the temperature and humidity system. We placed the sensor in a controlled climate and adjusted the temperature to different intervals. The results were very close to the set temperature. This system will help the greenhouse to provide the best possible care to their plants.

# Budget

$0.00

$100.00

$200.00

$300.00

$400.00

$500.00

$600.00

$700.00

Temp and Humidity | PLC | Lighitng | Display | Nutrient | CO2 and NO2 | Water Level

Team Spending

Proposed Actual

The team proposed to spend $1,387.85 in our project proposal. After all ordering complete the total budget concluded at $1,397.85, which is within .72% accuracy. With the budget being economically friendly, this will allow for future teams to expand upon the project. It will also allow the agricultural department to expand to their other greenhouse locations.

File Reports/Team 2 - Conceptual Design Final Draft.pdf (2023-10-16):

# Team 2 – Autonomous Greenhouse

Jaxson Billings
Computer and Electrical
Engineering Department
Tennessee Technological
University
Cookeville, TN
jlbillings42@tntech.edu

Jared Hooker
Computer and Electrical
Engineering Department
Tennessee Technological
University
Cookeville, TN
jahooker42@tntech.edu

Grant Hooper
Computer and Electrical
Engineering Department
Tennessee Technological
University
Cookeville, TN
gghooper42@tntech.edu

Noah Jones
Computer and Electrical
Engineering Department
Tennessee Technological
University
Cookeville, TN
rnjones42@tntech.edu

Bryan Rhoton
Computer and Electrical
Engineering Department
Tennessee Technological
University
Cookeville, TN
barhoton42@tntech.edu

Abstract—This report introduces Team 2’s idea for the 2023-2024 Capstone Design Project. The following report introduces the introduction to the problem followed by the objective and scope of the project. System description using block diagrams and further details, background information, constraints, and standards will also be established and discussed. The report will include professional considerations, possible solutions, obstacles, available solutions, implications, ethics, and responsibilities related to the solutions. Finally, the resources used for completing the project will be described including the components, funding, personnel, and timeline.

Keywords — Greenhouse, measurements, sensors, zones, temperature, humidity, PLC

I. INTRODUCTION
A. Formulated Problem

Team 2 plans on addressing the issue of automation within greenhouse environments utilizing a PLC system. The design that Team 2 will implement shall install two separate zones for the cultivation of different types of plant life. The design shall also include several sensors and exterior controls, such as fan controls and humidity sensors. This design shall activate fans within the greenhouse when an internal temperature of 85⁰F is reached. It shall also send an automated alert if carbon dioxide levels within the greenhouse reach either below 800ppm or below 1200ppm. The humidity sensors shall send an alert if the humidity level is outside of a manually set range, which will typically be 50-80% humidity. The design shall also contain an interface which will offer a customizable schedule for daily waterings as well as providing for a manual override in cases where excess watering is needed. Finally, the design shall offer soil nutrient and moisture sensors that will send alerts if the nutrient and moisture levels of the soil are not within a set ideal range provided by the customer.

B. Ethical Concerns

There are several ethical and professional concerns that are going to affect the design, implementation, and outcome of this project. Some examples of the ethical concerns are water usage efficiency, energy consumption, cybersecurity, and data asset protection. There are also several professional considerations that must be observed over the course of this project. One example would be preventative maintenance which is required when working with PLC systems. For more information about the professional considerations Team 2 is planning on observing, see the professional considerations section below. Team 2 also has several standards to consider in the design and implementation of the greenhouse project. Some examples of these standards are the NFPA 70 and the IEEE 160. For more information about the ethical and professional concerns as well as the standards Team 2 plans to address in this project please see the ethical, professional, and standards considerations section below.

C. Broader Impacts

There are multiple outcomes that can come from team 2’s automated greenhouse. Team 2’s greenhouse shall help to provide an easier workload for gardeners/farmers who have a lot to do already. This can help reduce human exhaustion and allow for more work to be done in a day, which in turn helps to provide more of a living to those selling plants being grown. Team 2 shall also provide a greenhouse with the means to grow non-native plants so that farmers/gardeners can have a variety of products or so that said plants do not invade and endanger the surrounding ecosystem.

II. SYSTEM DESCRIPTION

A. Block Diagram and Detail: Overhead


Figure 1. Block Diagram and Detail: Overhead

1. PLC Controller
This is the main control center for the entire system. It controls the five sub-systems by taking in data from the communications application, processing it, and sending back the desired response to the systems.
2. Water and Nutrient Control
The water and nutrient control subsystem shall consist of tanks of water with water level sensors that will relay the amount of water back to the communications application as well as a water pump to carry water to the different plants being grown. This subsystem will also include a manually mixed solution of fertilizer and nutrient injectors to deliver nutrients into planting soil. Inputted to the system will be the data from the PLC telling if the plants need water, nutrients, or fertilizer. It will output feedback to the database to be processed again.
3. Lighting
The lighting subsystem shall consist of several color changing LEDs controlled by a color changing remote that allows the user to input the desired color for the LEDs. The color of these lights will then be sent to the communications application to be reported to the user.
4. CO2 and Nitrogen Monitoring

This subsystem shall consist of a series of sensors that will continually monitor the level of carbon dioxide in the air as well as the percentage of nitrogen within the soil. If said level stray from a predetermined range, then the sensors will send an alert to the communications application to inform users of the deviation.
5. Communications Application
The communication application shall consist of a screen that displays the different levels and percentages we plan to monitor and will relay that information to the user.

Each individual subsystem will send their different data to the applications database to be presented to the user.
6. Temperature and Humidity Control
This subsystem shall consist of a temperature and humidity sensor that will monitor both parameters and will turn on the fans once the temperature reaches 85⁰F and both parameters shall be reported to the communications application.

Block Diagram and Detail: Water and Nutrient Control


Figure 2. Block Diagram and Detail: Water and Nutrient Control

1. Water & Nutrient Controller
This controller is what sends water and nutrients to the plants. From the PLC, data is sent telling the controller to turn on the water pump and/or nutrient injector and for how long.
2. Nutrient Injector
The nutrient injector gives liquid nutrients to plants by releasing it into the soil near their roots. The injector will be turned on by the water & nutrient controller for the programmed time, or until it is manually overridden.
3. Fertilizer/Water Mix
This is what will be sent through the nutrient injector. The solution will have to be mixed outside of the automation system. However, the amount of the solution given to the plants is determined by the controller or by manual override.
4. Water Pump
The water pump is what will pull the water and fertilizer mixture from the water tank for automated irrigation.
5. Water Tank
The water tank holds the water that will be manually mixed with the fertilizer to be delivered to the plants via the water pump.
Inputs:
1. Water
2. Optimal Fertilizer Mix
Outputs:
1. Water Level Percentage
2. Fertilizer Mix Percentage

Block Diagram and Detail: Lighting


Figure 3. Block Diagram and Detail: Lighting

1. Lighting Controller
This controller is what controls the different colored lights to the plants. From the PLC, data is sent telling the controller to turn on the light, what color the light with be, and for how long the light will be on.
2. Color Changing Grow Light
The grow light will turn on via the controller which will determine its color and for how long.
3. Color Changing Remote Control
This remote will manually change the color of the light turned on by the controller.
Inputs:
1. Desired Lighting Color
Outputs:
1. Desired Lighting Color

Block Diagram and Detail: CO2 and Nitrogen Monitoring


Figure 4. Block Diagram and Detail: CO2 and Nitrogen Monitoring

1. Soil Nitrogen Sensor
This sensor will report the percentage of nitrogen that is found in the soil and relay that information back to the communications application.
2. CO2 Sensor
The carbon dioxide sensor will report the concentration of carbon dioxide in the greenhouse’s atmosphere and will relay the information to the communications application.
Inputs:
1. CO2 Concentration
2. Soil Nitrogen Content
Outputs:
1. CO2 Concentration
2. Soil Nitrogen Content

Block Diagram and Detail: Communications Application


Figure 5. Block Diagram and Detail: Communications Application
1. Communications Application
The communication application will be the primary source of information for the users of this system. It will report all the information provided including temperature, humidity, water level, fertilizer percentage, nitrogen concentration, and carbon dioxide level.
2. Programming Software / Back-end
The back-end software will be the primary running source for the communications application. This software will allow the application to display the information it has been sent.
3. Database
The database will contain all relevant information that has been passed from the subsystems to the communications application.
4. Visualization & Screen
The screen will allow the information that is passed to the communications application to be displayed visually for the user of the system.

Inputs:
1. CO2 and Nitrogen Concentrations
2. Water and Fertilizer Mix Percentages
3. Lighting Color
4. Temperature and Humidity Percentages
Outputs:
1. All inputted information is relayed through the app

Block Diagram and Detail: Temperature and Humidity Control


Figure 6. Block Diagram and Detail: Temperature and Humidity Control
1. Temperature & Humidity Controller
This controller is what changes the temperature and humidity around the plants. From the PLC, data is sent telling the controller to turn on and whether to make it humid and/or hotter or colder.
2. Sensor
The sensor will determine whether the humidity or temperature exceeds the desired measurements and tell the controller whether to turn on and make changes.
Inputs:
1. Greenhouse Internal Temperature
2. Greenhouse Humidity
Outputs:
1. Greenhouse Temperature
2. Greenhouse Humidity
B. Constraints
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

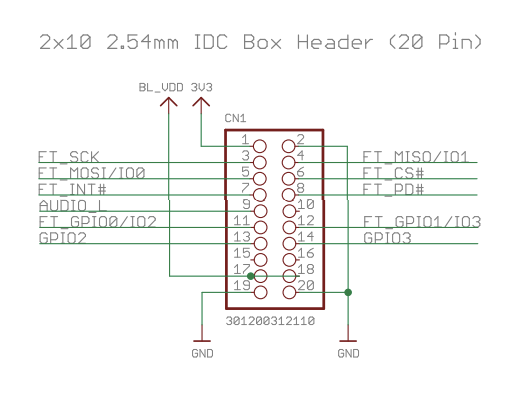
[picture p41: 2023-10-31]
Documentation/Images/Display Chip Schematic .png

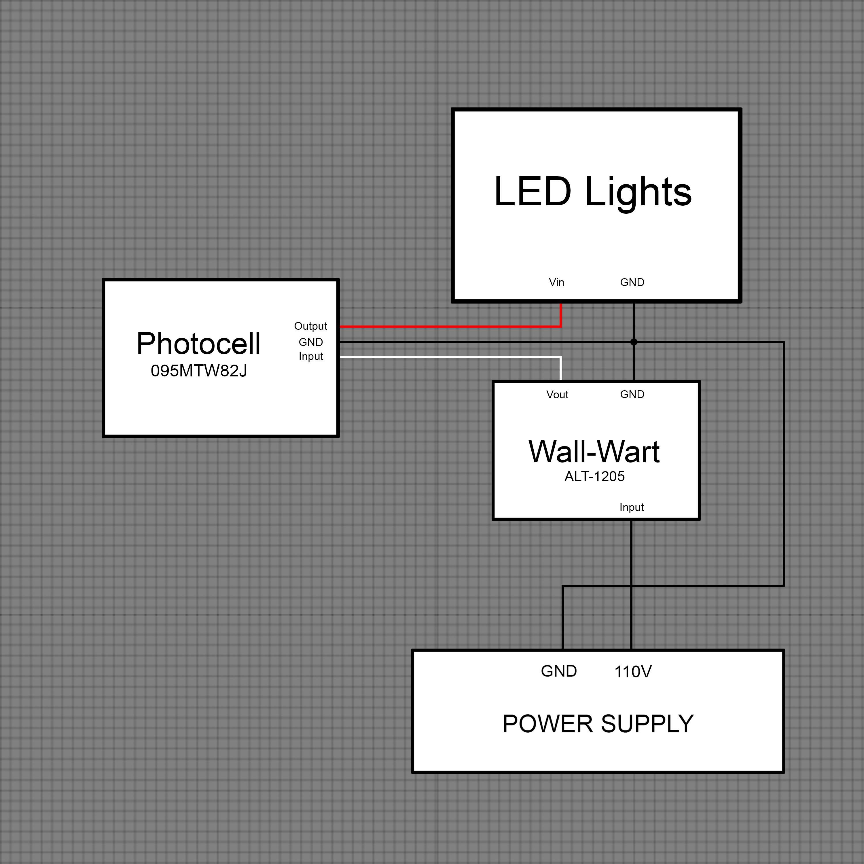
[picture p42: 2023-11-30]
Documentation/Electrical/Schematics/CADLightingSubsystem.jpg

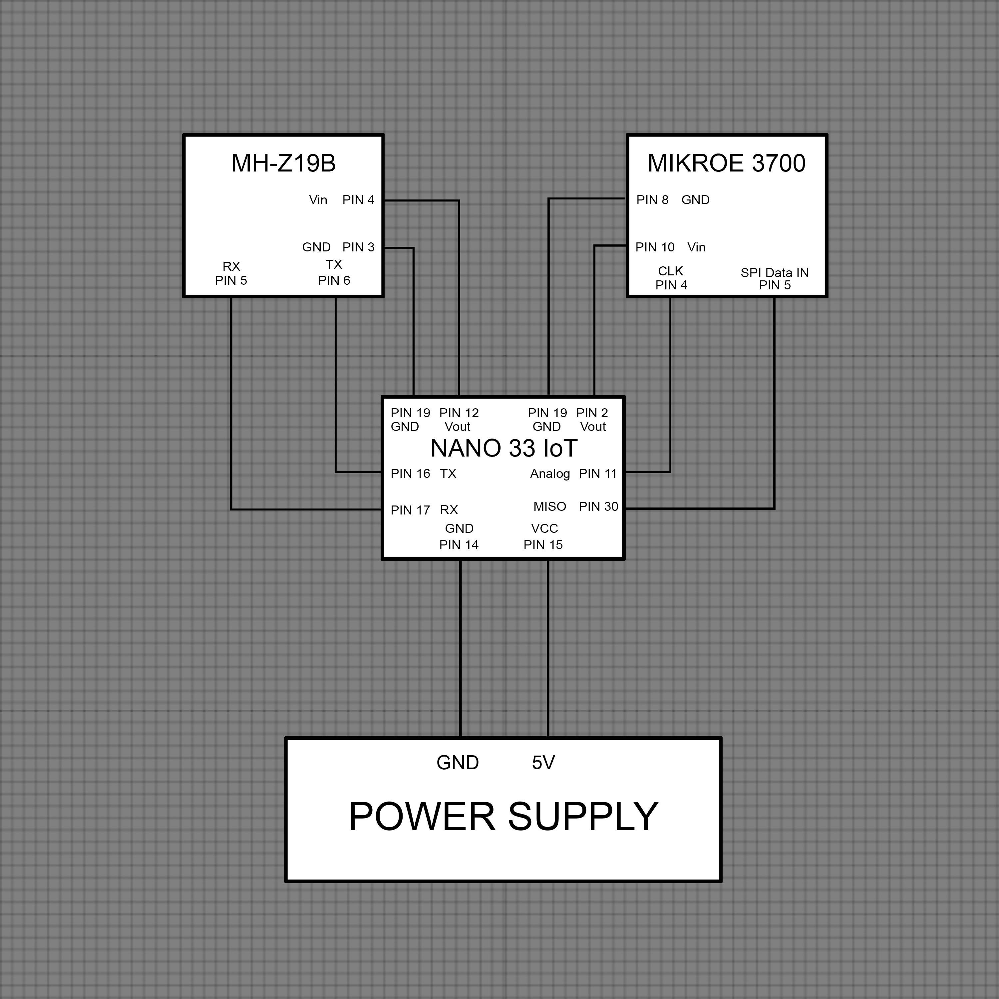
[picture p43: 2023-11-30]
Documentation/Electrical/Schematics/CADDrawingNitrogenSubsystem.jpg

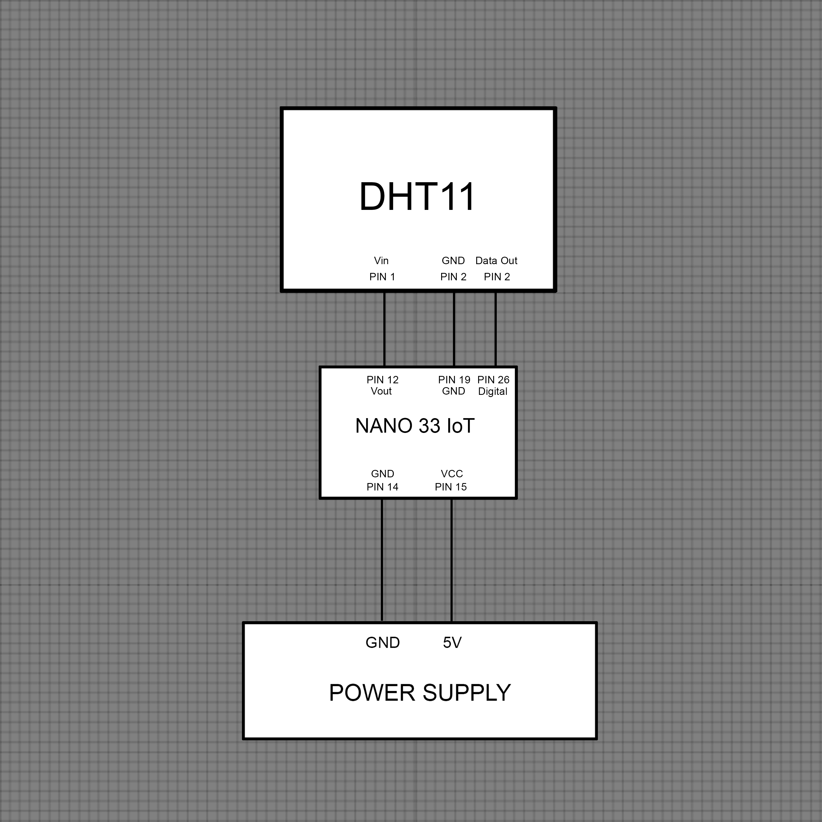
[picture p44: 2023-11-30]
Documentation/Electrical/Schematics/CADTemperature&HumiditySubsystem.jpg

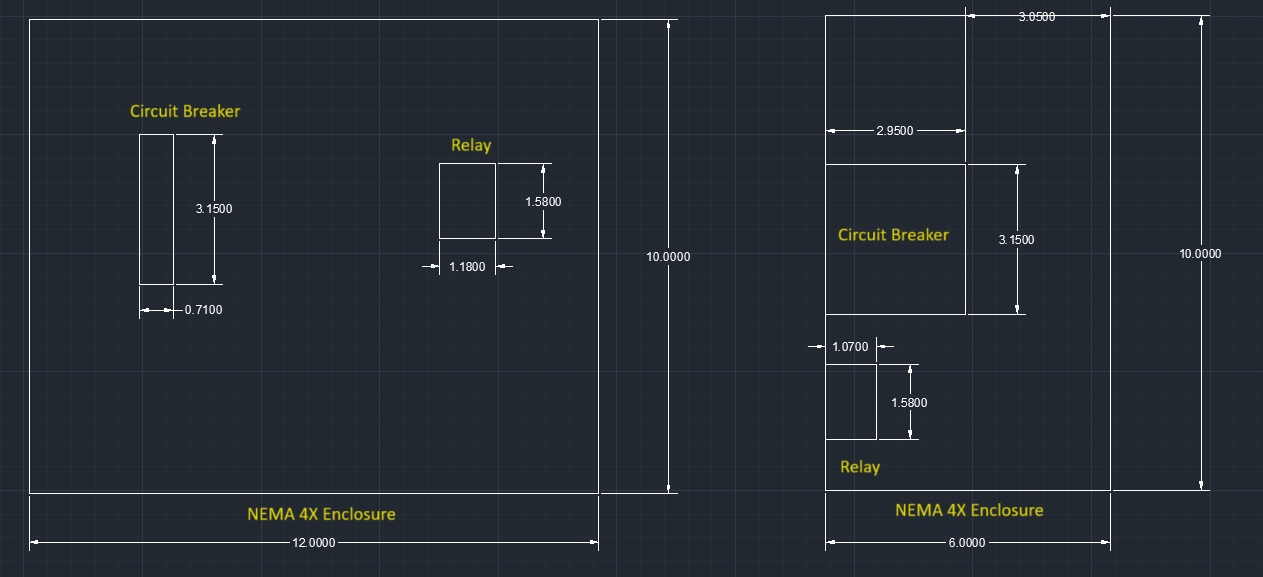
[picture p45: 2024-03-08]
Documentation/Images/Screenshot 2024-03-08 123324.jpg

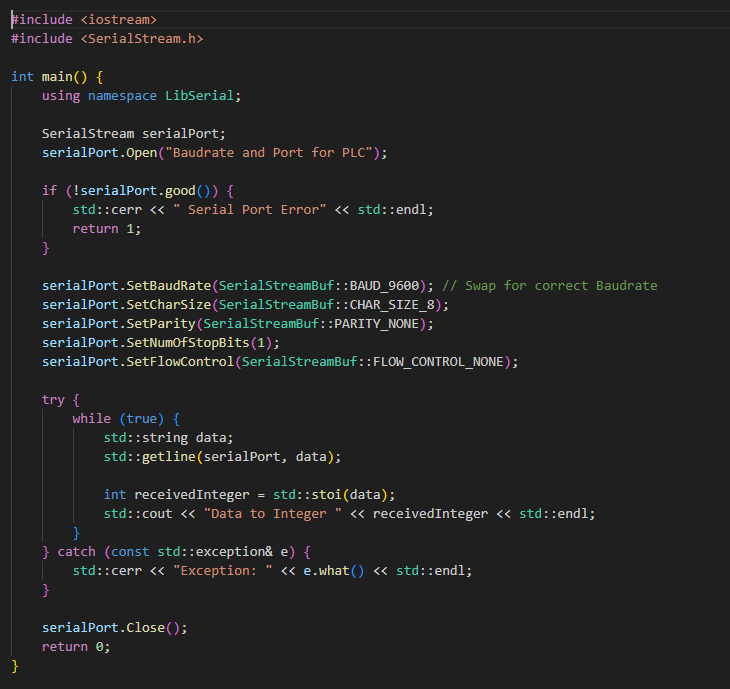
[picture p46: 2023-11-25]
Documentation/Images/Tx to Int Code.png

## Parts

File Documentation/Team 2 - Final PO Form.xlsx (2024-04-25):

Team 2 Greenhouse Project PO - Team Member: Robert Jones
Product Name | Description | Subsystem | Part Number | Manufacturer | Quantity | Price | Total Item Cost
Relay Module | 5V 40A | Lighting Control | BOBQ2RFW6G | LCLCTC | 1 | $18.90 | $18.90
Highydro LED Grow Light | Full Spectrum Growth Light | Lighting Control | B078B8HGRR | Highydro | 1 | $21.99 | $21.99
Nano 33 IoT | Bluetooth Board | Lighting Control, Water Level Monitoring, Temperature and Humidity Monitoring, Nutrient, and CO2 and NO2 Monitoring | ABX00027 | Arduino | 5 | $25.90 | $129.50
Clamp Lamp Light | Aluminum Reflector Bulb Socket | Lighting Control | B07H8G6PKX | VivoSun | 1 | $22.99 | $22.99
Circuit Breaker | 15A | Lighting Control | B0BFF6CX2X | DIHOOL | 1 | $13.99 | $13.99
Cable Glands | NPT 1/4" | Lighting Control | ‎NPT1/4(20P) | AIRIC | 1 | $11.99 | $11.99
Enclosure | 12x10x6" NEMA 4X | Lighting Control | HF0049-P12106 | TOCRETOARE | 1 | $49.99 | $49.99
10ft Extension Cord | 14-3 3 Prong Heavy Duty | Lighting Control | B0BWHYZV4V | HONDERSON | 1 | $12.99 | $12.99
30ft Extension Cord | 14-3 Heavy Duty Multiple Outlet | Lighting Control | B0BT56KZCR | Maximm | 1 | $32.99 | $32.99
Rubber Plug | Female Adapter | Lighting Control | 000-515PR-000 | Leviton | 1 | $10.97 | $10.97
PLC | Programmable Logic Controller | PLC | C2-03CPU | Automation Direct | 1 | $205.00 | $205.00
Power Supply | CLICK 100-240 VAC 24DC Supply | PLC | C0-01AC | Automation Direct | 1 | $63.00 | $63.00
MicroSD Card | Ultra microSDHC | PLC | SDSQUA4-032G-GN6MA | SanDisk | 1 | $7.65 | $7.65
Communication Module | TTL to RS232 | PLC | B07PFB4MHR | Generic | 1 | $15.99 | $15.99
Communication Cable | RS232 | PLC | DT-9006C 2M | Dtech | 1 | $10.96 | $10.96
Enclosure | SK-18 | PLC | SK-18 | Polycase | 1 | $41.17 | $41.17
Cable Glands | Gray Glands 1.53 x 1.19 x 1.19in | PLC | CG3 | Polycase | 2 | $2.86 | $5.72
Enclosure Mounting Kit | Kit for SK Enclosures 0.91 x 0.59 x 0.86 in | PLC | SK-99 | Polycase | 2 | $3.36 | $6.72
HMI | Human Machine Interface | Display | EA3-S3ML | C-more Micro | 1 | $280.00 | $280.00
Ethernet Cable | RJ45 male to RJ45 male, 3ft cable length | Display | C5E-STPBL-S3 | Automation Direct | 1 | $6.75 | $6.75
Temperature and Humidity Sensor | AHT20 Pin Module - I2C | Temperature and Humidity Monitoring | DHT20 | Adafruit | 2 | $7.51 | $15.02
Battery Holder | 4 AA Holder | Water Level Monitoring, Temperature and Humidity Monitoring, CO2 and NO2 Monitoring, and Nutrient | B07L9M6VZK | LAMPVPATH | 4 | $7.49 | $29.96
Batteries | 10 AA Batteries | Water Level Monitoring, Temperature and Humidity Monitoring, CO2 and NO2 Monitoring, and Nutrient | DURMN1500B10Z | Duracell | 4 | $13.33 | $53.32
Soil Probe | 7 in 1 Probe | Nutrient | CWT-SOIL-NPKPHCTH-S | ComWinTop | 1 | $81.39 | $81.39
Interface Module | RS485 Instrument Module | Water Level Monitoring and Nutrient | MAX485 TTL | Uxcell | 1 | $7.69 | $7.69
Zip Ties | 8" Zip Ties, 100 Pieces | Water Level Monitoring | 8inch 120lb | Bonison | 1 | $7.49 | $7.49
Dowel | 3/4" 3ft Dowel | Water Level Monitoring | 27835 | Madison Mill | 2 | $3.98 | $7.96
Water Level Sensor | Module JSN-SR04T Distance Measuring Transducer Sensor for Arduino | Water Level Monitoring | JSN-SR04T | DIYmore | 1 | $13.99 | $13.99
Enclosure | 5.12 x 3.70 x 2.24 in Waterproof Box | Water Level Monitoring | SK-15 | Polycase | 1 | $20.92 | $20.92
Breadboard | 400 Tie Point Mini Breadboard 5.5×8.2×0.85cm | Water Level Monitoring | B0135IQ0ZC | Qunqi | 1 | $5.99 | $5.99
Voltage Regulator | 6V Step-Up Regulator | Water Level Monitoring and Nutrient | U3V16F5 | Polulu | 2 | $4.95 | $9.90
Outdoor Enclosure | 16x12x16 in NEMA 4X Box | PLC | WB15.7X11X5.9 | Joinfworld | 1 | $49.99 | $49.99
Total Items Ordered | 47
Total Cost | $1272.88

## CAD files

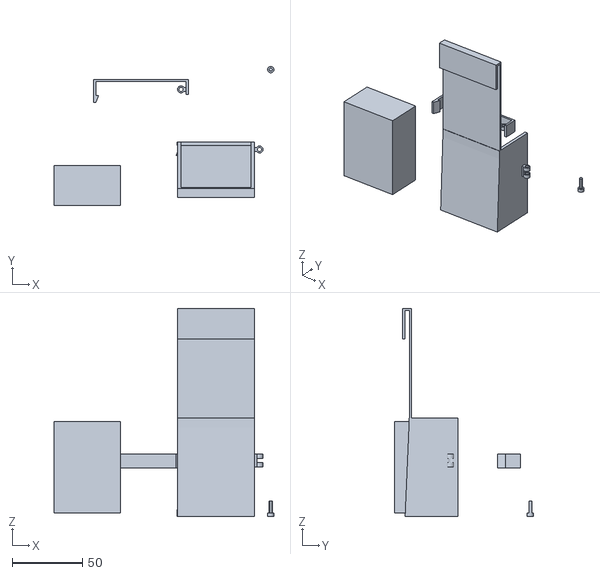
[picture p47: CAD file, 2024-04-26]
Documentation/3D Models/Brilliant Amur-Jarv.stl
156.1 x 98.7 x 147.6

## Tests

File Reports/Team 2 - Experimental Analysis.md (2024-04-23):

# Experimentation Assignment

## Subsystems and Constraints

### 1. Lighting Subsystem
   - Constraint 1: The lights must be able to shine for a minimum of 2 hours per day.
      - The lights are set to be on for a minimum of 2 hours per day. This was verfied by setting the Arduino to turn on and off every 2 minutes.
      - There is a slight variation in the results due to human error when recording with a stopwatch.
   
| Iterations | Light Status | Time (minutes) |
|---|---|---|
| 1 | ON | 1.00  |
| 2 | OFF | 2.00  |
| 3 | ON | 3.00  |
| 4 | OFF | 4.00  |
| 5 | ON | 5.01  |
| 6 | OFF | 6.01  |
| 7 | ON | 7.01  |
| 8 | OFF | 8.01  |
| 9 | ON | 9.02  |
| 10 | OFF | 10.02 |

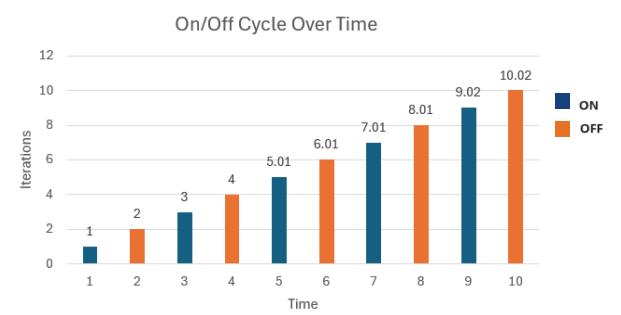
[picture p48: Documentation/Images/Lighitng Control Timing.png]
Lighting Timing


*Figure 1. Lighitng Timing Graph*

   - Constraint 2: The distance of the lights from the plants will have to be fully adjustable as the plants grow upward toward the lights.
      - The lights are powerful enough to keep from having to move them as the plants grow, but they are connected to a 10-foot cord that can move up and down.
   - Constraint 3: The HMI must give the user the ability to adjust how long the lights are on per day.
      - This must be between 2 and 6 hours, based on the current weather conditions or any other factors that may reduce UV light on the plants. The HMI is not functioning to allow for change to the lights on and off cycle but can be changed manually through the micro-USB port. 

### 2. CO2 and NO2 Subsystem
   - CO2 Constraint 1: MH-Z19B needs between 4.5-5.5V and at least 20mA to operate eﬃciently.
      - The soldered 5 volt pin (Pin 12) on the Arduino Nano 33 IoT supplies it with around 5.0V with a little variance to 4.9 to 5.1V.
   - CO2 Constraint 2: The sensor must turn on every 5 minutes to measure the amount of carbon dioxide present in the greenhouse.
     - Sensor code contains the WatchDog.sleep sleep mode function from the Adafruit SleepyDog library to cycle the system into sleep mode, reducing the operating current from 18mA to 6mA, every 5 minutes. The function itself only sleeps for 16 seconds, but when put into a for-loop with 19 iterations we meet our constraint of 5 minutes.
   - CO2 Constraint 3: Must alert the communications applications when above or below 400-2000 ppm to ensure proper plant growth.
      - The sensor correctly reads in the sensor data, but on a slightly higher level. For example, 400 ppm is represented as 40000 with the library we are using. That data is then checked to be above or below 40000 to 200000. If it is not within this range, a boolean true is sent over BLE. If it is within this range then the boolean remains false.
      - An experiment was ran with 20 iterations. The experiment was ran inside of a household room at normal temperature. The expected CO2 ppm is between 300-400ppm in a household. The table below shows the data gathered.
    
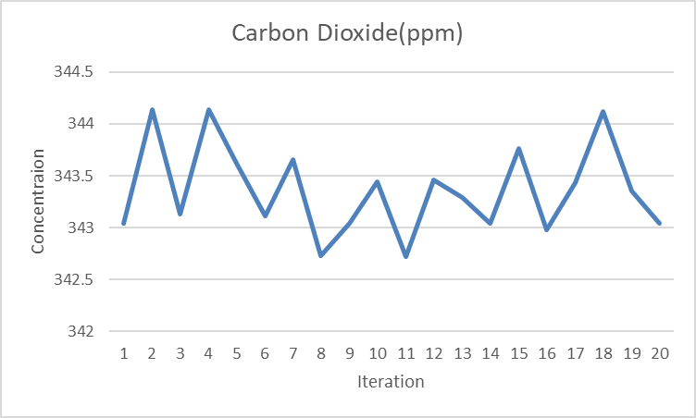
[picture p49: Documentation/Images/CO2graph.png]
C02 Graph


*Figure 2. Carbon Dioxide Levels for the MH-Z19B Sensor*

| Iterations | Carbon Dioxide (ppm) |
|---|---|
| 1 | 343.04 |
| 2 | 344.14 |
| 3 | 343.13 |
| 4 | 344.14 |
| 5 | 343.62 |
| 6 | 343.11 |
| 7 | 343.66 |
| 8 | 342.73 |
| 9 | 343.04 |
| 10 | 343.44 |
| 11 | 342.72 |
| 12 | 343.46 |
| 13 | 343.29 |
| 14 | 343.04 |
| 15 | 343.76 |
| 16 | 342.98 |
| 17 | 343.43 |
| 18 | 344.12 |
| 19 | 343.35 |
| 20 | 343.04 | 

   - NO2 Constraint 1: MIKROE-3700 needs between 3.3-5V to operate efficiently.
      - The MIKROE-3700's Vcc pin is connected directly to the 3.3V pin (Pin 2) on the Arduino Nano 33 IoT which supplies the 3.3V required.
   - NO2 Constraint 2: Must alert when above Nitrogen Dioxide level exceeds 9 ppb.
      - The MIKROE-3700 does alert when levels are not in the correct range. However, the NO2 sensor readings are not correct. The sensor sends data over via SPI, but then received by the Arduino, it only outputs 0 or 65535.00. It is believed that this is the sensor's way of sending the minimum or maximum value allowed. Obviously, this is not the data expected. The current MIKROE-3700 documentation is not very in depth and does not give information on how to receive the 12-bit ADC that is supposed to be sent and received. There also are no libraries for the MIKROE-3700 for the Arduino Nano 33 IoT, so we can't see how the sensor is being read this way either. 

### 3. Temperature and Humidity Subsystem
   - Constraint 1: The sensor shall have 2.5-5.5 V to operate correctly. 20 iterations were taken for the voltage. For each iteration, a voltage very close to 3.3 volts were observed. A table and graph for the voltage at each iteration is given below.

| Iterations | Voltage (V) |
|---|---|
| 1 | 3.278 |
| 2 | 3.279 |
| 3 | 3.265 |
| 4 | 3.267 |
| 5 | 3.268 |
| 6 | 3.278 |
| 7 | 3.278 |
| 8 | 3.276 |
| 9 | 3.267 |
| 10 | 3.282 |
| 11 | 3.278 |
| 12 | 3.273 |
| 13 | 3.278 |
| 14 | 3.278 |
| 15 | 3.275 |

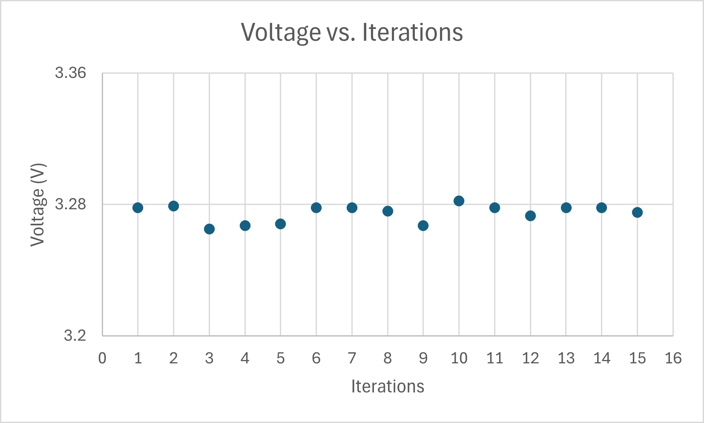
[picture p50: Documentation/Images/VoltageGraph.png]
Voltage Graph


*Figure 3. Voltage Values Test*

   - Constraint 2: Sensor uses 3.2mW when on, and 0 W when in sleep mode. We tested the voltage multiple times and received a voltage range of 3.2-3.4 volts every time. We also tested for current and received measurements between 1.0-1.1 mA. If we calculate power by multipling voltage by current, we see that we have a range of 3.2-3.74 mW. When it sleep mode the power uses 0 watts.
   - Constraint 3: Temperature range of 0-50°C (32-122°F) and humidity range of 20-90%. While testing in a room temperature environment, we see a range of +- 2 degrees Celsius maximum and a range of +- 1%rH. For our testing, we were in a room that was 20 degrees Celsius and a humidity of 41 %rH. Here is the data set we got for 18 trials.

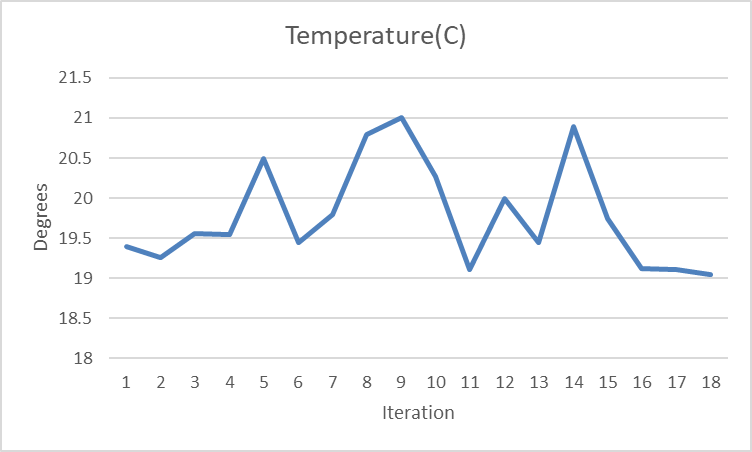
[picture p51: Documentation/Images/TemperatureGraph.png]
Temperature Graph


*Figure 4. Temperature Graph Values for DHT20 Sensor*

| Iterations | Temperature values (Celsius) |
|---|---|
| 1 | 19.40 |
| 2 | 19.26 |
| 3 | 19.56 |
| 4 | 19.55 |
| 5 | 20.49 |
| 6 | 19.44 |
| 7 | 19.80 |
| 8 | 20.79 |
| 9 | 21.01 |
| 10 | 20.27 |
| 11 | 19.11 |
| 12 | 19.99 |
| 13 | 19.45 |
| 14 | 20.89 |
| 15 | 19.75 |
| 16 | 19.12 |
| 17 | 19.11 |
| 18 | 19.05 |

We find that the sum over the count is 356.04/18 which equals 19.78. Next, we will show the data gathered by the humidity sensor.

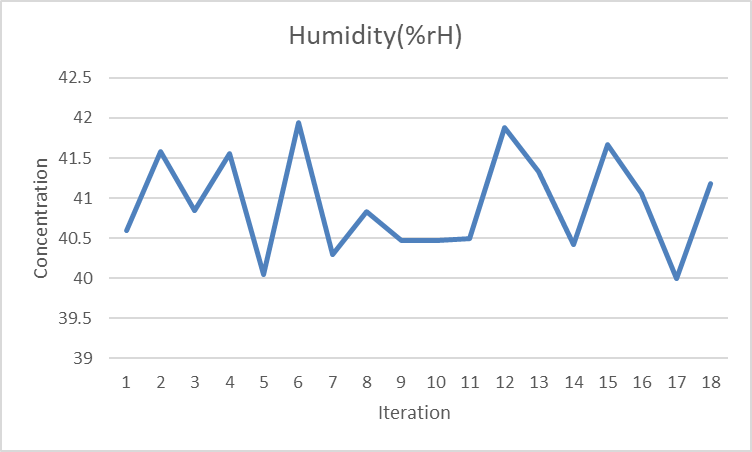
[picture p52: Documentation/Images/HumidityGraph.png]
Humidity Graph


*Figure 5. Humidity Graph Values for DHT20 Sensor*

| Iterations | Humidity values (%rH) |
|---|---|
| 1 | 40.59 |
| 2 | 41.58 |
| 3 | 40.84 |
| 4 | 41.56 |
| 5 | 40.05 |
| 6 | 41.94 |
| 7 | 40.30 |
| 8 | 40.83 |
| 9 | 40.47 |
| 10 | 40.47 |
| 11 | 40.49 |
| 12 | 41.88 |
| 13 | 41.33 |
| 14 | 40.42 |
| 15 | 41.67 |
| 16 | 41.06 |
| 17 | 40.00 |
| 18 | 41.18 |

   We find that the sum over the count is 736.66/18 which equals roughly 40.93.
     
   - Constraint 4: Sampling period of greater than or equal to 2 seconds, so it is set to be 10 seconds to allow for extra time. We added the Arduino libraries "delay()" function, which allows for input of an integer which is understood to be in milliseconds,  with a value of 10000 to allow for 10 extra seconds to achieve this.

### 4. Water Level Subsystem
   - Constraint 1:  The transfer of data between the sensors and the Arduino must be below 3 seconds for accurate and reliable monitoring of water level. After Testing we got the following data:

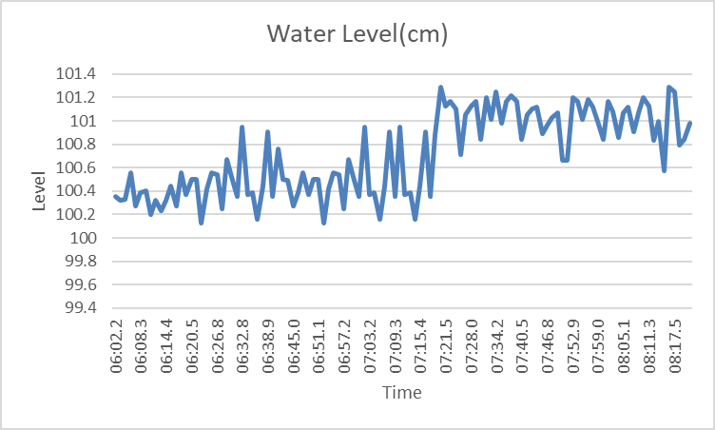
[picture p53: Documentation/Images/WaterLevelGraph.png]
Water Level Graph


*Figure 6. Water Level Graph Values for the Sensor*

| Time Stamp | Distance (cm) |
|---|---|
| 17:06:02.247  | 100.35 |
| 17:06:03.464  | 100.32 |
| 17:06:04.681  | 100.33 |
| 17:06:05.902  | 100.56 |
| 17:06:07.110  | 100.27 |
| 17:06:08.320  | 100.39 |
| 17:06:09.539  | 100.40 |
| 17:06:10.789  | 100.20 |
| 17:06:11.971  | 100.32 |
| 17:06:13.192  | 100.23 |
| 17:06:14.411  | 100.32 |
| 17:06:15.654  | 100.44 |
| 17:06:16.862  | 100.27 |
| 17:06:18.075  | 100.56 |
| 17:06:19.288  | 100.37 |
| 17:06:20.493  | 100.50 |
| 17:06:21.889  | 100.50 |
| 17:06:23.102  | 100.13 |
| 17:06:24.320  | 100.42 |
| 17:06:25.534  | 100.56 |
| 17:06:26.753  | 100.54 |
| 17:06:27.972  | 100.25 |
| 17:06:29.190  | 100.67 |
| 17:06:30.398  | 100.49 |
| 17:06:31.618  | 100.35 |
| 17:06:32.820  | 100.95 |
| 17:06:34.061  | 100.37 |
| 17:06:35.282  | 100.39 |
| 17:06:36.494  | 100.16 |
| 17:06:37.713  | 100.44 |
| 17:06:38.932  | 100.91 |
| 17:06:40.143  | 100.35 |
| 17:06:41.364  | 100.76 |
| 17:06:42.577  | 100.50 |
| 17:06:43.794  | 100.49 |
| 17:06:45.010  | 100.27 |
| 17:06:46.217  | 100.39 |
| 17:06:47.430  | 100.56 |
| 17:06:48.649  | 100.37 |
| 17:06:49.868  | 100.50 |
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

   - Total time elapsed:
      - Start time: 17:06:02.247
      - End time: 17:08:21.110
      - Convert both times to milliseconds:
      - Start time in milliseconds: 61562247 ms
      - End time in milliseconds: 61761110 ms
      - Total time elapsed: 61761110 ms - 61562247 ms = 198863 ms
      - Number of intervals between readings: 114 readings, so 114 - 1 = 113 intervals.
      - Average time per reading:
      - Average time = Total time elapsed / Number of intervals
      - Average time = 198863 ms / 113 = 1760.56 ms

   - Average Distance
      - Average distance = Sum of all Distances / Number of readings
      - Average distance =  11365.74 / 113 = 100.58 cm
      - The sensor was set to 100 cm above the ground. Therefore it was off by 0.58 cm

   - Constraint 2: Must be able to accurately sense when water level drops below 1/3 of the max to signal more water is needed to be added to the reservoir.
        - The sensor reads the data correctly, but struggles to change the water level distance from the ground at a consistent rate. For example, if the ground is 100 cm away and we drastically reduce the water level, the sensor does not read the change in water level accurately.

   - Constraint 3: Must be durable enough to continue function while wet for an indefinite amount of time.
        - Sensor is waterproof and can withstand the harsh conditions of the environment it is placed in, which in this case includes constantly being close to the water.
        - After the sensor was exposed to water in 10 seperate trials it was still able to comunicate and send water level data.

   - Constraint 4: Must be cheap and easily replaceable in the chance the user requires a new sensor.
        - Sensor is $12.99, while maintaining a high quality and accuracy in a cost effective price range.

### 5. Nutrient Subsystem
   - Constraint 1: Must have an operational voltage between 4.5V and 30V.
        - Sensor and translator operate with a voltage of 6V supplied from the battery pack which is well within the range of required voltages.
   
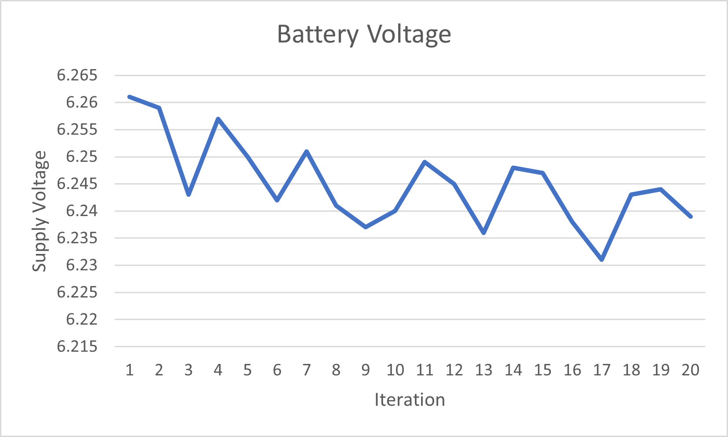
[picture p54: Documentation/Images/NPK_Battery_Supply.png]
NPK Battery Analysis


*Figure 7. Nutrient System Voltage Supply*

| Iterations | Voltage Supply(V) | 
| --- | --- |
| 1 | 6.261 |
| 2 | 6.259 |
| 3 | 6.243 |
| 4 | 6.257 |
| 5 | 6.250 |
| 6 | 6.242 |
| 7 | 6.251 |
| 8 | 6.241 |
| 9 | 6.237 |
| 10 | 6.240 |
| 11 | 6.249 |
| 12 | 6.245 |
| 13 | 6.236 |
| 14 | 6.248 |
| 15 | 6.247 |
| 16 | 6.238 |
| 17 | 6.231 |
| 18 | 6.243 |
| 19 | 6.244 |
| 20 | 6.239 |
   - Constraint 2: Sensors must turn on every 5 minutes to provide soil NPK, pH and moisture information.
        - Sensor code contains the WatchDog.sleep sleep mode function from the Adafruit SleepyDog library to cycle the system into sleep mode, reducing the operating current from 18mA to 6mA, every 5 minutes. The function itself only sleeps for 16 seconds, but when put into a for-loop with 19 iterations we meet our constraint of 5 minutes.
    
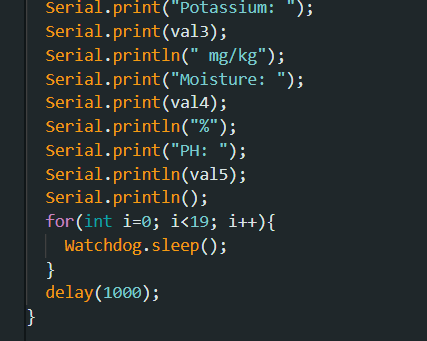
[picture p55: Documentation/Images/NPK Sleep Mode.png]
NPK Sleep Mode


*Figure 8. Sleep Mode Function Code for NPK Sensor*

   - Constraint 3: Must accurately measure soil moisture in a range of 0-100% to allow for optimum plant growth with ±3% to ±5% accuracy.
      -  The data below shows that the sensor will send moisture data for for the first few iterations and then will cease communication with the arduino.
   - Constraint 4: Must accurately measure nitrogen levels in the soil within a range of 50-300 mg/kg to allow for optimum plant growth with no more than ±10% accuracy.
      - The data below shows that the sensor communicates the levels of nitrogen in the soil with the arduino with a small degree of accuracy with only a few readings being outside the normal range of 10-50 mg/kg 
   - Constraint 5: Must accurately measure phosphorus levels in the soil within a range of 5-90 mg/kg with no more than ±10% accuracy.
      - The data below shows that the sensor sends phosphorus data to the arduino but there is very little accuracy in the readings with most readings being outside the normal range of 200-1500 mg/kg. 
   - Constraint 6: Must accurately measure potassium levels in the soil within a range of 50-240 mg/kg with no more than ±10% accuracy.
      - The data below shows that sensor sends data for potassium readings but is not accurate since almost no readings are within the normal range, additionally the sensor stopped communicating data for potassium at iteration 14 indicated by the sudden jump to 255 mg/kg which was most likely caused by the sensor being subjected to direct sunlight.
   - Constraint 7: Must accurately measure soil pH levels within a range of 5-8.5pH with an accuracy of ±0.01 pH to ±0.5 pH.
      - The data below shows that the sensor will not communicate pH data with the arduino which is caused by the lack of documentation on the sensor's register addressing for the values of the readings.

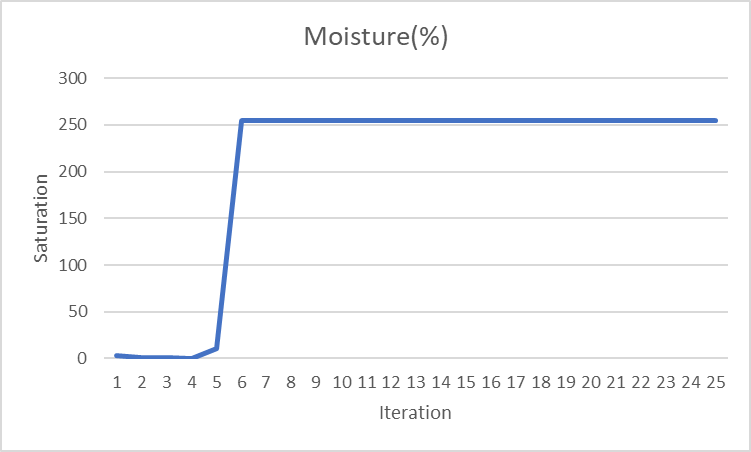
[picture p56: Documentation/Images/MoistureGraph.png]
Moisture Graph


*Figure 9. Mositure Graph Values for NPK Sensor*

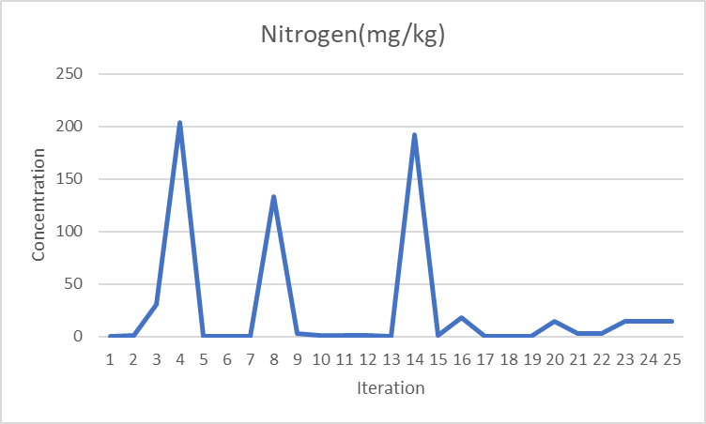
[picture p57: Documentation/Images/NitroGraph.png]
Nitrogen Graph


*Figure 10. Nitrogen Graph Values for NPK Sensor*

Phosphorus Graph

*Figure 11. Phosphorus Graph Values for NPK Sensor*

Potassium Graph

*Figure 12. Potassium Graph Values for NPK Sensor*

Soil pH

*Figure 13. Soil pH Graph Values for NPK Sensor*

### 6. HMI Subsystem
   - Constraint 1: The HMI shall be capable of receiving and displaying sensor data from various sources within the greenhouse, including nutrient levels, humidity, temperature, CO2, and NO2 levels.
        - HMI is able to connect to the PLC and display any value in the PLC with the associated address.
   - Constraint 2: Communication between the HMI and PLC must be robust and reliable to ensure real-time monitoring of sensor data.
        - HMI is able to display the one second timer in the PLC toggling on and off while running.
   - Constraint 3: The HMI shall have sufficient screen resolution and clarity to display sensor readings in an easily understandable format, including any alerts or notifications.
        - HMI has characters large enough to be able to be read clearly
   - Constraint 4: Power supply for the HMI shall provide stable wattage at 1.05W to ensure uninterrupted operation of the display system.
        - The HMI is safely provided power via the C0-01AC power supply.

### 7. PLC Subsystem
   - Constraint 1: The PLC scan time shall be able to scan fast enough to accommodate the desired sampling rate for all subsystem sensors.
      - These sensors will be sending data every 5 minutes. The PLC is able to scan fast enough to recieve data every 5 minutes.
   - Constraint 2: The PLC shall have compatible communication ports to allow for available programming.
        - The PLC has multiple ports including the Ethernet and micro USB ports for programming. 
   - Constraint 3: The PLC shall be able to operate in 30% to 95% relative non–condensing humidity to ensure its suitability for deployment in greenhouse environmental conditions without risking damage due to moisture.
      - PLC is operating in a weather-proof panel box.
   - Constraint 4: The PLC shall be able to input data from at least 3 Arduino Nano 33 IoT.
      - The subsystem has been designed where 5 other arduino's addressed are searched for by one central Arduino. All cases have been successful when searching and finding all online and transmitting Arduinos. The central Arduino then fills in a "value" buffer with the attributes of each peripheral. The addresses are searched for in a specific order and the buffer has a size of 5, allowing for the new data from the Arduino's to overwrite the previous data from the same Arduino. This is then sent to a TTL-RS232 converter. The converter is hooked up to a RS232 cord that communicates to the PLC. The PLC does receive this data, as the receive light on the PLC lights up whenever we try to transmit. An oscciloscope can also be used by hooking up the probe to the RX/TX pin and reads in spikes up voltages whenever we transmit. However, the PLC Ladder Logic has not been completed and does not receive and store the data. 
   - Constraint 5: The PLC shall be able to log data every hour for at least 1 month.
      - Once the PLC Ladder Logic is completed and stores the data in the Addresses specified, the .csv file can be set to store at specifed amount of time. This is the data-logging feature on the AutomationDirect CLICK Programming Tool. The PLC also has an SD Card that these .csv files can be saved on. The PLC can have up to 99999 .csv files saved before it deletes the oldest and saves it's new data. This is ready to be implemented when the PLC correctly stores data in the "Data View".
   - Constraint 6: The power supply shall incorporate overcurrent protection and overvoltage protection to provide protection mechanisms for safeguarding connected equipment and ensuring the reliability of the power distribution system.
        - The C0-01AC power suuply provides the required protections for overcurrent and overvoltage.

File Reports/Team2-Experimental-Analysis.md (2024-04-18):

# Experimentation Assignment

## Subsystems and Constraints

### 1. Lighting Subsystem
   - Constraint 1: The lights must be able to shine for a minimum of 2 hours per day.
      - The lights are set to be on for a minimum of 2 hours per day.
   - Constraint 2: The distance of the lights from the plants will have to be fully adjustable as the plants grow upward toward the lights.
      - The lights are powerful enough to keep from having to move them as the plants grow, but they are connected to a 10-foot cord that can move up and down.
   - Constraint 3: The HMI must give the user the ability to adjust how long the lights are on per day.
      - This must be between 2 and 6 hours, based on the current weather conditions or any other factors that may reduce UV light on the plants. The HMI is not functioning to allow for change to the lights on and off cycle but can be changed manually through the micro-USB port. 

### 2. CO2 and NO2 Subsystem
   - CO2 Constraint 1: MH-Z19B needs between 4.5-5.5V and at least 20mA to operate eﬃciently.
      - The soldered 5 volt pin (Pin 12) on the Arduino Nano 33 IoT supplies it with around 5.0V with a little variance to 4.9 to 5.1V.
   - CO2 Constraint 2: The sensor must turn on every 5 minutes to measure the amount of carbon dioxide present in the greenhouse.
     - Sensor code contains the WatchDog.sleep sleep mode function from the Adafruit SleepyDog library to cycle the system into sleep mode, reducing the operating current from 18mA to 6mA, every 5 minutes. The function itself only sleeps for 16 seconds, but when put into a for-loop with 19 iterations we meet our constraint of 5 minutes.
   - CO2 Constraint 3: Must alert the communications applications when above or below 400-2000 ppm to ensure proper plant growth.
      - The sensor correctly reads in the sensor data, but on a slightly higher level. For example, 400 ppm is represented as 40000 with the library we are using. That data is then checked to be above or below 40000 to 200000. If it is not within this range, a boolean true is sent over BLE. If it is within this range then the boolean remains false.
      - An experiment was ran with 20 iterations. The experiment was ran inside of a household room at normal temperature. The expected CO2 ppm is between 300-400ppm in a household. The table below shows the data gathered.

| Iterations | Carbon Dioxide (ppm) |
|---|---|
| 1 | 343.04 |
| 2 | 344.14 |
| 3 | 343.13 |
| 4 | 344.14 |
| 5 | 343.62 |
| 6 | 343.11 |
| 7 | 343.66 |
| 8 | 342.73 |
| 9 | 343.04 |
| 10 | 343.44 |
| 11 | 342.72 |
| 12 | 343.46 |
| 13 | 343.29 |
| 14 | 343.04 |
| 15 | 343.76 |
| 16 | 342.98 |
| 17 | 343.43 |
| 18 | 344.12 |
| 19 | 343.35 |
| 20 | 343.04 | 
   - NO2 Constraint 1: MIKROE-3700 needs between 3.3-5V to operate efficiently.
      - The MIKROE-3700's Vcc pin is connected directly to the 3.3V pin (Pin 2) on the Arduino Nano 33 IoT which supplies the 3.3V required.
   - NO2 Constraint 2: Must alert when above Nitrogen Dioxide level exceeds 9 ppb.
      - The MIKROE-3700 does alert when levels are not in the correct range. However, the NO2 sensor readings are not correct. The sensor sends data over via SPI, but then received by the Arduino, it only outputs 0 or 65535.00. It is believed that this is the sensor's way of sending the minimum or maximum value allowed. Obviously, this is not the data expected. The current MIKROE-3700 documentation is not very in depth and does not give information on how to receive the 12-bit ADC that is supposed to be sent and received. There also are no libraries for the MIKROE-3700 for the Arduino Nano 33 IoT, so we can't see how the sensor is being read this way either. 

### 3. Temperature and Humidity Subsystem
   - Constraint 1: The sensor shall have 2.5-5.5 V to operate correctly. The sensor is given the constant voltage of 3.3V from Pin 2 on the Arduino Nano 33 IoT
   - Constraint 2: Sensor uses 3.2mW when on, and 0 W when in sleep mode. We tested the voltage multiple times and received a voltage range of 3.2-3.4 volts every time. We also tested for current and received measurements between 1.0-1.1 mA. If we calculate power by multipling voltage by current, we see that we have a range of 3.2-3.74 mW. When it sleep mode the power uses 0 watts.
   - Constraint 3: Temperature range of 0-50°C (32-122°F) and humidity range of 20-90%. While testing in a room temperature environment, we see a range of +- 2 degrees Celsius maximum and a range of +- 1%rH. For our testing, we were in a room that was 20 degrees Celsius and a humidity of 41 %rH. Here is the data set we got for 18 trials. 

| Temperature values |
|--------------------|
| 19.40              |
| 19.26              |
| 19.56              |
| 19.55              |
| 20.49              |
| 19.44              |
| 19.80              |
| 20.79              |
| 21.01              |
| 20.27              |
| 19.11              |
| 19.99              |
| 19.45              |
| 20.89              |
| 19.75              |
| 19.12              |
| 19.11              |
| 19.05              |

   We find that the sum over the count is 356.04/18 which equals 19.78. Next, we will show the data gathered by the humidity sensor.
| Humidity values |
|-----------------|
| 40.59           |
| 41.58           |
| 40.84           |
| 41.56           |
| 40.05           |
| 41.94           |
| 40.30           |
| 40.83           |
| 40.47           |
| 40.47           |
| 40.49           |
| 41.88           |
| 41.33           |
| 40.42           |
| 41.67           |
| 41.06           |
| 40.00           |
| 41.18           |

   We find that the sum over the count is 736.66/18 which equals roughly 40.93.
     
   - Constraint 4: Sampling period of greater than or equal to 2 seconds, so it is set to be 10 seconds to allow for extra time. We added the Arduino libraries "delay()" function, which allows for input of an integer which is understood to be in milliseconds,  with a value of 10000 to allow for 10 extra seconds to achieve this.

### 4. Water Level Subsystem
   - Constraint 1:  The transfer of data between the sensors and the Arduino must be below 3 seconds for accurate and reliable monitoring of water level. After Testing we got the following data:
        - Total time elapsed:
             - Start time: 17:06:02.247
             - End time: 17:08:21.110
             - Convert both times to milliseconds:
             - Start time in milliseconds: 61562247 ms
             - End time in milliseconds: 61761110 ms
             - Total time elapsed: 61761110 ms - 61562247 ms = 198863 ms
             - Number of intervals between readings: 114 readings, so 114 - 1 = 113 intervals.
             - Average time per reading:
             - Average time = Total time elapsed / Number of intervals
             - Average time = 198863 ms / 113 = 1760.56 ms

   - Constraint 2: Must be able to accurately sense when water level drops below 1/3 of the max to signal more water is needed to be added to the reservoir.
        - The sensor reads the data correctly, but struggles to change the water level distance from the ground at a consistent rate. For example, if the ground is 100 cm away and we drastically reduce the water level, the sensor does not read the change in water level accurately.

   - Constraint 3: Must be durable enough to continue function while wet for an indefinite amount of time.
        - Sensor is waterproof and can withstand the harsh conditions of the environment it is placed in, which in this case includes constantly being close to the water.

   - Constraint 4: Must be cheap and easily replaceable in the chance the user requires a new sensor.
        - Sensor is $12.99, while maintaining a high quality and accuracy in a cost effective price range.

### 5. Nutrient Subsystem
   - Constraint 1: Must have an operational voltage between 4.5V and 30V.
        - Sensor and translator operate with a voltage of 6V supplied from the battery pack which is well within the range of required voltages.
   - Constraint 2: Sensors must turn on every 5 minutes to provide soil NPK, pH and moisture information.
        - Sensor code contains the WatchDog.sleep sleep mode function from the Adafruit SleepyDog library to cycle the system into sleep mode, reducing the operating current from 18mA to 6mA, every 5 minutes. The function itself only sleeps for 16 seconds, but when put into a for-loop with 19 iterations we meet our constraint of 5 minutes.
   - Constraint 3: Must accurately measure soil moisture in a range of 0-100% to allow for optimum plant growth with ±3% to ±5% accuracy.
   - Constraint 4: Must accurately measure nitrogen levels in the soil within a range of 50-300 mg/kg to allow for optimum plant growth with no more than ±10% accuracy.
   - Constraint 5: Must accurately measure phosphorus levels in the soil within a range of 5-90 mg/kg with no more than ±10% accuracy.
   - Constraint 6: Must accurately measure potassium levels in the soil within a range of 50-240 mg/kg with no more than ±10% accuracy.
   - Constraint 7: Must accurately measure soil pH levels within a range of 5-8.5pH with an accuracy of ±0.01 pH to ±0.5 pH.
        - For constraints 3 through 7, there was no datasheet and very little documentation on the sensor itself so the register addresses for the sensor values were not able to be found. Despite this limitation we used the register values of a similar sensor and were still unable to get the sensor to communicate with the arduino. The sensor will however send a constant value of 255 for all measures.

### 6. HMI Subsystem
   - Constraint 1: The HMI shall be capable of receiving and displaying sensor data from various sources within the greenhouse, including nutrient levels, humidity, temperature, CO2, and NO2 levels.
        - HMI is able to connect to the PLC and display any value in the PLC with the associated address.
   - Constraint 2: Communication between the HMI and PLC must be robust and reliable to ensure real-time monitoring of sensor data.
        - HMI is able to display the one second timer in the PLC toggling on and off while running.
   - Constraint 3: The HMI shall have sufficient screen resolution and clarity to display sensor readings in an easily understandable format, including any alerts or notifications.
        - HMI has characters large enough to be able to be read clearly
   - Constraint 4: Power supply for the HMI shall provide stable wattage at 1.05W to ensure uninterrupted operation of the display system.
        - The HMI is safely provided power via the C0-01AC power supply.

### 7. PLC Subsystem
   - Constraint 1: The PLC scan time shall be able to scan fast enough to accommodate the desired sampling rate for all subsystem sensors.
      - These sensors will be sending data every 5 minutes. The PLC is able to scan fast enough to recieve data every 5 minutes.
   - Constraint 2: The PLC shall have compatible communication ports to allow for available programming.
        - The PLC has multiple ports including the Ethernet and micro USB ports for programming. 
   - Constraint 3: The PLC shall be able to operate in 30% to 95% relative non–condensing humidity to ensure its suitability for deployment in greenhouse environmental conditions without risking damage due to moisture.
      - PLC is operating in a weather-proof panel box.
   - Constraint 4: The PLC shall be able to input data from at least 3 Arduino Nano 33 IoT.
      - The subsystem has been designed where 5 other arduino's addressed are searched for by one central Arduino. All cases have been successful when searching and finding all online and transmitting Arduinos. The central Arduino then fills in a "value" buffer with the attributes of each peripheral. The addresses are searched for in a specific order and the buffer has a size of 5, allowing for the new data from the Arduino's to overwrite the previous data from the same Arduino. This is then sent to a TTL-RS232 converter. The converter is hooked up to a RS232 cord that communicates to the PLC. The PLC does receive this data, as the receive light on the PLC lights up whenever we try to transmit. An oscciloscope can also be used by hooking up the probe to the RX/TX pin and reads in spikes up voltages whenever we transmit. However, the PLC Ladder Logic has not been completed and does not receive and store the data. 
   - Constraint 5: The PLC shall be able to log data every hour for at least 1 month.
      - Once the PLC Ladder Logic is completed and stores the data in the Addresses specified, the .csv file can be set to store at specifed amount of time. This is the data-logging feature on the AutomationDirect CLICK Programming Tool. The PLC also has an SD Card that these .csv files can be saved on. The PLC can have up to 99999 .csv files saved before it deletes the oldest and saves it's new data. This is ready to be implemented when the PLC correctly stores data in the "Data View".
   - Constraint 6: The power supply shall incorporate overcurrent protection and overvoltage protection to provide protection mechanisms for safeguarding connected equipment and ensuring the reliability of the power distribution system.
        - The C0-01AC power suuply provides the required protections for overcurrent and overvoltage.

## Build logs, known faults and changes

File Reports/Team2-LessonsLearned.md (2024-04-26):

# Team 2 Lessons Learned

## Member and Individual Lessons Learned/Classes Applied

### Noah Jones

- What went well:
    - For me, the main thing that went well was providing power to the lighting, PLC, and HMI subsystems. After realizing that using an extension cord was our best option during the building of the lighting system, it was easy to duplicate for the other two systems. Soldering and wiring of the systems also went well as I had previous experience doing so in previous courses.
- What did not go well:
    - The PLC and HMI systems did not go well due our lack of knowledge of working with them and also how little time we had to get them going. 
- Problems:
    - The only issue I had was finding a relay for my system. Acquiring a relay with such a low control voltage and high output voltage was much more difficult than I expected.
- What would you do differently?
    - If I could go back and do this course over again, the main thing that I would do differently would be to focus on using larger, more powerful LEDs from the start. I spent way too much time trying to design a system that met my previous constraints instead of just changing the constraints themselves, which overall led to a better project.
- Best Practices:
    - Some of the best practices I have acquired from this course happened in the last month of this year-long course. From electrical safety, to soldering, to wiring, I feel as if these are what I will always look back on and be glad I had to experience this class.
- Words of wisdom:
    - To future capstone groups, always read the data sheets, always. If a component you are looking to use has a bad datasheet or even not one at all, there is a reason. It is worth spending a few extra dollars on a component for which you have more information on. `
- New knowledge or skills:
    - The knowledge that I have gained from this course I will use for the rest of my career. These things include writing a formal and technical report, programming, working for a customer, and most importantly, how to be an engineer.

### Grant Hooper

- What went well:
    - The HMI coding itself went pretty well as well as constructing the hardware for the water level monitoring subsystem. Along with eventually getting the HMI and PLC to communicate after an ungodly amount of time fiddling with them.
- What did not go well:
   - The connection between the hub arduino and the PLC never did fully work even though all signed pointed to them working.
- Problems:
   - The arduino hub and PLC would not comminicate properly. The arudinos power out pins weren't working properly. The water sensor wasn't consistent at first.
- What would you do differently?
    - I probably would have been more "flowy" than i guess stubborn is the best way to put it. I would have been more willing to look at other options rather than try to brute force something that doesn't work.
- Best Practices:
    - My best practices were electrical safety with the PLC and learning to be more detail oriented. 
- Words of wisdom:
    - Do not just go with the first component or solution you find before finding more and comparing all options for your best result.
- New knowledge or skills:
    - I learned more about building a system but espescially a PLC system and learning to code Automation direct PLC ladder logic.

### Jared Hooker

- What went well:
    - The building of each subsystem onto a soldered breadboard went very well. We were able to successfully make sure that each sensor on the breadboards were getting the correct voltage needed. Troubleshooting for many of the subsystems I did also went well, and I was able to fix a few issues that occurred by taking a strategic process of what might be the problem.
- What did not go well:
    - The temperature and humidity subsystem had problems reading in the correct value from the sensor, but this problem was fixed after resoldering a couple of the pins on the board.
- Problems:
    - One problem was that we ordered breadboards that required much more soldering than anticipated due to the each section not being connected. A few of our breadboards had to be resoldered because of this.
- What would you do differently?
    - I would buy better breadboards, and I would also research more on the best board to use for certain sensors.
- Best Practices:
    - I good practice that I obtained was double checking my work, as well as being more concise with my work.
    -  My communication skills were improved tremendously.
    -  I gained some experience in coding from assisting my teammates with their work, and also gained some information on how bluetooth works.
- Words of wisdom:
    - Teamwork is essential in order to truly have success in this class. Your team is there to help you, so it is okay if you do not know something. Everyone has different strengths and weaknesses, so do not be afraid to ever ask for assistance.
    - Always make sure to give your best effort in everything you do in this class, and take pride in your work.
    - Start early on every report so that you have enough time to think through everything you plan to do in this class.
- New knowledge or skills:
    - This class gave me a good idea of what the real world is like, and how to think like an engineer rather than a student. It allowed me to become better at problem solving and critical thinking.
    - I was able to become a better communicator due to the amount of teamwork and meetings that were required throughout the two semesters of Capstone Design.

### Jaxson Billings

- What went well:
    - What went well was the construction and overall the programming of all Arduino's. BLE advertising and receiving addresses, serviceUUIDs, CharacteristicUUIDs, Attributes, and Values all worked phenomenally with both the peripheral and central Arduino's. Wiring of the circuits, getting everything the correct voltage to each component,  and getting them on solderless breadboards also went well.
- What did not go well:
    - What did not go well was the interface and protocols used with most sensors. Many of the components bought had very poor documentation and not much information about use. Also, getting the PLC to recieve RS232 seemed like an easy enough task, but time ran low and we were not able to figure out the correct connection/ladder logic.
- Problems:
    - The problems we incountered were libraries not being compatiable with the board manager used for the Arduino Nano 33 IoT, the PLC signaling it was receiving via RS232 but not took in the data, the NO2 sensor only ever sent high or low depending on if it was receiving enough voltage, and  the Arduino's digital set pin HIGH worked a minority of the time.
- What would you do differently?
    - If I could do thing differently, I would make sure that 100% of the sensors bought had solid data sheets, as well as documentation and compatiable libraries with the Arduino being used. I would also think about switching away from the Arduino Nano 33 IoT because most sensors are made for other older Arduino's and are not compatiable with the SAMD Board Manager. I would better utilize the example projects given whenever a library is downloaded. I would order better solderless breadboards to allow for connections and less finicky voltages.
- Best Practices:
    - I've picked up some valuable practices, like thoroughly making sure code is written to be reusable and well documented, researching topics before committing to ideas, carefully reviewing datasheets or product documentation, ensuring products align with my specific requirements before making commitments, and not hesitating to ask numerous questions, even if it means reaching out to the product manufacturer.
- Words of wisdom:
    - Do all your research. Have full confidence in what you are buying and know before hand how it is going to be programmed, what tools may be needed, how the connections will be not only theoretically but realistically.
- New knowledge or skills:
    - I learned more from this class than almost every other class I have taken. It bettered my skills in C, thought me how to truly make connections on a system without relying on soldered breadboards, as well as how to use Arduino IDE.

### Bryan Rhoton

- What went well:
    - For my part of the project what went well was the construction and testing of my system. As we tested we learned that the register address values I was using were wrong and I had to go back and fix them as best I could through trial and error. Another part of the process that went well for me was the coding of the system and being able to assist my teammates in the coding, construction and connection identification of their systems.
- What did not go well:
    - What did not go well for me was the design aspect of my system. Not only having to search the internet for what felt like days on end to find a sensor that would fit within our constraints and budget but also to find an adequate voltage regulator that would do exactly what we wanted it to.
- Problems:
    - One unanticipated problem that occured was the delay of my sensor being shipped and another was the unavailability of tbe voltage regulator that we had originally intended to use. Yet another problem was the lack of adequate documentation and datasheets for the sensor and other components of my system making it incredibly difficult to accurately code and test. One final problem that occured for my system was that the regulators we ordered, not the originals we had planned to order but a replacement, did not output voltage as they were meant to when connected to power the regultor would simply do nothing no matter how many configurations and tests we attempted the regulators simply would not output voltage.
- What would you do differently?
    - Personally what I would do differently would be to research npk sensors and voltage regulators much more in depth before I had begun to design with them. The lack of documentation and reliable sensors available make it difficult to make constraints for this kind of system let alone deliver on them so more research before hand would have been incredibly helpful.
- Best Practices:
    - Some best practices I learned were to always fully research a topic before you commit to the idea, always fully read the datasheet or documentation of products you plan to use, ensure products fit your specific needs before commiting to them and ask as many questions as needed even if you have to contact the manufactuer of the product you plan on using.
- Words of wisdom:
    - My words of wisdom would be to conduct research on your proposed problem, project or system before you commit to it. Ensure that there is adequate documentation for whatever you choose to do so you don't have to essentially make it up as you go along and research along the way.
- New knowledge or skills:
    - In capstone I increased my knowledge base of Arduino coding and libraries. I learned the very basic idea of BLE communication and functionality. I also learned very basic knowledge of how plcs and hmis work and are operated. Finally I learned an immense amount about the operation of and calculations for voltage regulators and their different functions.

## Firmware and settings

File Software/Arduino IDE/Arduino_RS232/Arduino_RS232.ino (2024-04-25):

#include <ArduinoBLE.h>

struct DeviceInfo {
  String address;
  String uuid;
};

// Define an array of devices you want to interact with
DeviceInfo devices[] = {
  //{"e0:5a:1b:7a:c4:0e", "180D"},
  {"78:21:84:ab:ef:26", "180C"} // DHT20 Sensor
  //{"e0:5a:1b:79:72:4e", "180E"} //NO2 Sensor
  //{"e0:5a:1b:79:72:4e", "180F"} //CO2 Sensor
  //{"e0:5a:1b:7a:c4:0e", "180A"} //NPK Sensor
  //{"e0:5a:1b:77:e7:e6", "180B"} //Water Level Sensor
};
int currentDeviceIndex = 0;

void setup() {
  Serial.begin(9600, SERIAL_8N1);
  while (!Serial);

  Serial1.begin(9600, SERIAL_8N1);
  while(!Serial1);

  if (!BLE.begin()) {
    Serial.println("starting Bluetooth® Low Energy module failed!");
    while (1);
  }    
  BLE.setLocalName("Central");
  Serial.println("Bluetooth® Low Energy Central scan");
  BLE.scanForAddress("78:21:84:ab:ef:26"); // Start scanning without specifying an address
}

void loop() {
  // Check if we've gone through all devices
  if (currentDeviceIndex >= (sizeof(devices) / sizeof(devices[0]))) {
    Serial.println("Processed all devices. Restarting...");
    currentDeviceIndex = 0; // Optionally restart or halt the program
    //return; // Uncomment to stop after processing all devices
  }

  BLEDevice peripheral = BLE.available();

  if (peripheral) {
    // Get the current target device info
    DeviceInfo& targetDevice = devices[currentDeviceIndex];

    // Check if the found peripheral matches the target address
    if(peripheral.address() == targetDevice.address) {
      Serial.println("Discovered a peripheral");
      Serial.println("-----------------------");
      Serial.print("Address: ");
      Serial.println(peripheral.address());

      Serial.print("Local Name: ");
      Serial.println(peripheral.localName());

      Serial.print("UUID: ");
      Serial.print(peripheral.advertisedServiceUuid());
      Serial.println();

      BLE.stopScan();

      // Assuming explorerPeripheral function is adapted to use DeviceInfo
      explorerPeripheral(peripheral, targetDevice.uuid);

      // Move to the next device
      currentDeviceIndex++;
      BLE.scan(); // Restart scanning for the next device
    }
  }
}

void explorerPeripheral(BLEDevice peripheral, String uuic) {
  // connect to the peripheral
  Serial.println("Connecting ...");

  if (peripheral.connect()) {
    Serial.println("Connected");
  } else {
    Serial.println("Failed to connect!");
    return;
  }

  // discover peripheral attributes
  Serial.println("Discovering attributes ...");
  if (peripheral.discoverAttributes()) {
    Serial.println("Attributes discovered");
  } else {
    Serial.println("Attribute discovery failed!");
    peripheral.disconnect();
    return;
  }

  // loop the services of the peripheral and explore each
  for (int i = 0; i < peripheral.serviceCount(); i++) {
    BLEService service = peripheral.service(i);
    exploreService(service);
  }

  Serial.println();

  // we are done exploring, disconnect
  Serial.println("Disconnecting ...");
  peripheral.disconnect();
  Serial.println("Disconnected");
}

void exploreService(BLEService service) {
  // Filter for services with UUIDs 180D and 180C
  const char* serviceUUID = service.uuid();
  if(strcmp(serviceUUID, "180c") == 0 || strcmp(serviceUUID, "180b") == 0){
    Serial.print("Service ");
    Serial.println(serviceUUID);

    // Loop the characteristics of the service and explore each
    for (int i = 0; i < service.characteristicCount(); i++) {
      BLECharacteristic characteristic = service.characteristic(i);
      // Filter for characteristic with UUID 2A57
      if(strcmp(characteristic.uuid(), "2a57") == 0){
        exploreCharacteristic(characteristic);
      }
    }
  }
}

void exploreCharacteristic(BLECharacteristic characteristic) {
  // Print the UUID and properties of the characteristic
  Serial.print("\tCharacteristic ");
  Serial.print(characteristic.uuid());

  // Check if the characteristic is readable
  if (characteristic.canRead()) {
    // Read the characteristic value
    characteristic.read();

    if (characteristic.valueLength() > 0) {
      // Print out the value of the characteristic
      Serial.print(", value 0x");
      printData(characteristic.value(), characteristic.valueLength());

      // Send the data to PLC
      sendDataToPLC(characteristic.value(), characteristic.valueLength());
      delay(2000);
    }
  }
  Serial.println();
}

// Define the function to send data to the PLC via TTL to RS232 Module
void sendDataToPLC(const unsigned char data[], int length) {
  // Send data to the PLC via TTL to RS232 Module connected to Rx/Tx
  Serial1.write(data, length); // Use Serial1 to send data
  Serial1.write('X'); //Cut Off

  // For debugging, you might want to print what you're sending to the Serial Monitor as well
  Serial.println("\n");
  Serial.println("Sending to PLC: ");
  for (int i = 0; i < length; i++) {
    unsigned char b = data[i];
    if (b < 16) {
      Serial.print("0");
    }
    Serial.print(b, HEX);
  }
  Serial.println();
}

void printData(const unsigned char data[], int length) {
  for (int i = 0; i < length; i++) {
    unsigned char b = data[i];

    if (b < 16) {
      Serial.print("0");
    }

    Serial.print(b, HEX);
  }
}

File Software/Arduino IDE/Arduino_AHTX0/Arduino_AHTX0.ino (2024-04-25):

#include <Adafruit_AHTX0.h>
#include <ArduinoBLE.h>

// Create an instance of the AHTX0 class
Adafruit_AHTX0 aht;

String t, h;

BLEService customService("180c");
BLEStringCharacteristic ble_temperature("2a57", BLERead | BLENotify, 13);

void readValues();

void setup() {
  Serial.begin(9600);
  // Initialize the DHT20 sensor
  while(!Serial);
  if(!BLE.begin()){
    Serial.println("BLE Failed to Initiate");
    delay(500);
    while(1);
  }
  /*while (!aht.begin()) {
    Serial.println("Failed to initialize DHT20, please check if the sensor is connected properly.");
    delay(1000);
  }*/

    BLE.setLocalName("Arduino Temperature Sensor");
    
    // Setting BLE Service Advertisment
    BLE.setAdvertisedService(customService);
    
    // Adding characteristics to BLE Service Advertisment
    customService.addCharacteristic(ble_temperature);

    // Adding the service to the BLE stack
    BLE.addService(customService);

    // Start advertising
    BLE.advertise();

}

void loop() {
  BLEDevice central = BLE.central();
  if(central){
    Serial.print("Connected to central: ");
    Serial.println(central.address());
    while(central.connected()){
      delay(200);
      readValues();

      ble_temperature.writeValue("Temp: " + t);

      //ble_temperature.writeValue(h);

      Serial.print("\n");
      delay(1000);
    }
  }
}

void readValues(){
  sensors_event_t humidity, temp;

  aht.getEvent(&humidity, &temp);

  float temperature = temp.temperature;
  //float humidityValue = humidity.relative_humidity;

  t = String(temperature);
  //h = String(humidityValue);

  Serial.print("Temp: ");
  Serial.println(t);
  Serial.print("Humidity: ");
  Serial.println(h);

  delay(5000);
}

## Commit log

2023-11-02 Buildable Schematic Water Level
2023-11-02 Create Temperature & Humidity Monitoring - Signoff.md
2023-11-02 Uploaded Nutrient Schematic
2023-11-08 Update CO2 & NO2 Monitoring Subsystem - Signoff.md
    Updated Buildable Schematic
    Updated Microcontroller to Arduino Nano 33 IoT
    Updated BoM
2023-11-09 Update CO2 & NO2 Monitoring Subsystem - Signoff.md
    Updated Schematic
2023-11-15 Update NutrientSubsystemSignoff.md
    Edited Schematic as well as Constraints and Analysis
2023-11-16 Update NutrientSubsystemSignoff.md
    Further Edited Schematic
2023-11-16 Water Level Subsystem Schematic
2023-11-16 Update Temperature & Humidity Monitoring - Signoff.md
2023-11-16 Update NutrientSubsystemSignoff.md
    Updated Sensor Power Analysis
2023-12-07 Update NutrientSubsystemSignoff.md
    Added information on sensor power supply
2024-01-25 Team2-Signoff-Water Level Monitoring Subsystem - Signoff.md
    added constraints to the water level sensor
2024-02-29 Update Team2-Signoff-DisplaySubsystem.md
    Added picture of area where HMI is to be mounted
2024-03-09 Update Lighting Control - Signoff.md
    In the power supply analysis:
    Line 2 - breaker proof
    Line 3 - relay proof
    Line 4 - extension cord proof
2024-04-25 Arduino Files
2024-04-26 Rename Team 2 - Final PO Form.xlsx to Team 2 - Final PO Form.xlsx
    [Team 2 - Final PO Form.xlsx]
2024-04-26 Moved BoM
    [Team 2 - Final PO Form.xlsx]
